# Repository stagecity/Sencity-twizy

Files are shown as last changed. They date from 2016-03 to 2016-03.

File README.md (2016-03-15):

# Sencity-twizy

This repository contains programs, documentation and other stuff needed by the project Sencity to work with the car.
This work is from the school [TELECOM Nanncy](http://telecomnancy.univ-lorraine.fr)

## Sencity project
Sencity is an educational collaborative and innovative project around the Internet of Things and
smart city. It relies on the development of an experimental platform to allow students to design,
develop and test new smart services in interaction with citizens and their environment. As part
of the project, an electric car was bought to collect data across the city.

## Environment 
### Operating system
It is recommanded to use Ubuntu LTS (14.04).
Download it here : http://www.ubuntu.com/download/desktop

Follow the installation instructions : http://www.ubuntu.com/download/desktop/install-ubuntu-desktop

**You will need to use the serial, so ya have to add your user to the group dialout**
 
### Network 
#### LIDAR
The Velodyne LIDAR Puck send data over ethernet with UDP packet.
You will need to set up your ethernet interface as follow :
 * IP address: 192.168.1.70 (70 as example, any number except 201 works)
 * Gateway: 255.255.255.0

**Don't forget to allow incoming UDP packet from 192.168.1.201 in your firewall**

#### GoPro
To remotly control the GoPro, you will need to configure it as a WiFi hotspot and then connect it.
If you use the one that was configured during the internship, use the following login :
 * SSID : TNTwizy1
 * Passphrase (WPA-PSK) : telecom54

#### WiFi
In order to perform WiFi scan with the ROS WiFi module, you need to set the setuid on iwlist :
```bash
chmod +s /sbin/iwlist
```

### Robot Operating System
#### Installation
Robot Operating System is the main component of this work.
Follow intructions from this page : http://wiki.ros.org/indigo/Installation/Ubuntu
You have to install the following dependancies :

```bash
apt-get install  ros-indigo-desktop-full ros-indigo-imu-filter-madgwick ros-indigo-rviz-imu-plugin ros-indigo-nmea-msgs libpcap-dev
```

#### Workspace
To set your workspace up, follow the ROS wiki :
http://wiki.ros.org/ROS/Tutorials/InstallingandConfiguringROSEnvironment

#### To learn
You should learn ROS basis from their Tutorials :
http://wiki.ros.org/ROS/Tutorials

#### Compilation
In the src folder, copy all packages from the folder ROS/.

Then compile them with ROS build system :
```bash
catkin_make -DCMAKE_BUILD_TYPE=RelWithDebInfo gps_msgs_generate_messages wifi_msgs_generate_messages
catkin_make -DCMAKE_BUILD_TYPE=RelWithDebInfo
```

To install files in your workspace use the following command :

```bash
catkin_make -DCMAKE_BUILD_TYPE=RelWithDebInfo install
```
### Install script
To setup your environment, you can just install the Operating system and execute [setup.sh](setup.sh).
```bash
wget "https://github.com/stagecity/Sencity-twizy/raw/master/setup.sh"
chmod +x setup.sh
./setup.sh
```

### Arduino
You will need arduino to read data from the Inertial Measurement Unit
Official website : https://www.arduino.cc/

The recommanded IDE is [Arduino IDE](https://www.arduino.cc/en/Main/Software)

You may want to read its [manual](https://www.arduino.cc/en/Guide/Environment)!

#### Librarie
You will have to copy the folder "Arduino/libraries/MPU9250" as "Mpu9250Spi"in your arduino libraries folder.

#### Compilation
Open the sketch Arduino/imu/imu.ino with arduino IDE and upload it on your board.

## Data specification
see [Data.md](Data.md)

## Hardware specification and configuration
see [Hardware.md](Hardware.md)

## Use
To start the saving system :
ROS only :
```bash
roslaunch twizy save.launch maxSize:=MaximalFileSizeInByte outputDir:=/path/to/record/folder/ wifiPort:=wifiCardName gpsPort:=/dev/tty{ACM|USB}[0-9] imuPort:=/dev/tty{ACM|USB}[0-9]
```
ROS and GoPro acquisition :
```bash
./launch.sh maxSize:=MaximalFileSizeInByte outputDir:=/path/to/record/folder/ wifiPort:=wifiCardName gpsPort:=/dev/tty{ACM|USB}[0-9] imuPort:=/dev/tty{ACM|USB}[0-9]
```

To view the recorded data :
```bash
roslaunch twizy viewBag.launch file:=/path/to/recorde/Rosbag_yyyy-mm-dd-hh-mm-ss.bag
```

You will find more arguments in the ROS twizy package dcumentation.

Other launch files are avaible : 
 * saveAndView.launch : record data and show them in real-time
 * streamView.launch : show sensors data in real-time
 * view.launch : launch ROS viewing software with configurations

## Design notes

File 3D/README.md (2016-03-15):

# 3D Model for printer

This folder contains 3D model made with the software OpenScad.
They are intended to be printed with a 3D printer!

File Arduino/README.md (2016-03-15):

# Arduino work

You will find here libraries and sketches for Arduino that are used in the project.

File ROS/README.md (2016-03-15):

# ROS modules

This folder contains modules for ROS needed or developed for the project.

 * gps, imu, velodyne_savedata and wifi contain modules developed for sensors
 * velodyne is a fork heavily modified for this project
 * velodyne_savedata is a module for velodyne to store LIDAR data in file
 * twizy contains the ROS core of this project
 * rviz_satellite is a module used to see GPS position on OpenStreetMaps maps in rviz
 * serial is a dependancie librarie for gps and imu

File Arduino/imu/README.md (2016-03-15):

# Arduino sketch for IMU

This sketch is intended to collect IMU data with the MPU9250-SPI library and to send it to ROS over serial 

Open it with Arduino IDE and upload to your board

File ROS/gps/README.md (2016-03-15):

# ROS GPS modules

 * gps : metapackage for all this modules
 * gps_msgs : messages definition used by these modules
 * gps_driver : get serial data from GPS and publish NMEA sentences in ROS message
 * gps_parser : parse NMEA sentences and publish data in ROS message
 * gps_fix : publish position-velocity-time fix for ROS

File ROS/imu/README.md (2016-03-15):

# ROS IMU modules

 * imu : metapackage for all this modules
 * imu_driver : get serial data from Arduino and publish ROS messages for IMU
 * imu_save : save IMU data in binary file

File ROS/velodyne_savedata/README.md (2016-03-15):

Overview
========

Velodyne_savedata is a package supporting `Velodyne high
definition 3D LIDAR VLP16`.

It works with and uses the following :

.. _ROS: http://www.ros.org
.. _Velodyne: http://www.ros.org/wiki/velodyne
.. _`Velodyne high definition 3D LIDARs`: http://www.velodynelidar.com/lidar/lidar.aspx

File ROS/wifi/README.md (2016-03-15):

# ROS WiFi modules

 * wifi : metapackage for all this modules
 * wifi_msgs : messages definition used by these modules
 * wifi_driver : get serial data from GPS and publish NMEA sentences in ROS message
 * wifi_save : publish position-velocity-time fix for ROS

**WiFi driver require the software iwlist. The setuid bit must be set!**
By example :
```bash
chmod +s /sbin/iwlist
```

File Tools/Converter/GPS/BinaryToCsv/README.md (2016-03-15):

# GPS binary to CSV tool

This tool is intended to convert saved file from ROS gps_save module to CSV file format.

## How to compil :
```bash
make
```

## How to use :
```bash
./imuBinToCsv /path/to/file.bin
```
The new file will be : /path/to/file.bin.csv
**Be aware that no check is performed to verify the input file is correct!**

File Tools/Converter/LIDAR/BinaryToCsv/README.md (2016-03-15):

# LIDAR binary to CSV tool

This tool is intended to convert saved file from ROS velodyne_savedata module to CSV file format.

## How to compil :
```bash
make
```

## How to use :
```bash
./lidarBinToCsv /path/to/file.bin
```
The new file will be : /path/to/file.bin.csv
**Be aware that no check is performed to verify the input file is correct!**

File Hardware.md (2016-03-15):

# Hardware 
Here is described the hardware.

## Garmin GPS 18 LVC

Seller site : [GPS 18x OEM | Garmin](https://buy.garmin.com/en-US/US/oem/sensors-and-boards/gps-18x-oem/prod27594.html)

[Driver and Software](https://www8.garmin.com/support/collection.jsp?product=010-00321-31)

Please refer to APPENDIX E of [Garmin 18.pdf](Docs/GPS/Garmin 18.pdf), and download [SNSRXCFG](https://www8.garmin.com/support/download_details.jsp?id=4053) to configure the GPS.

### Configuration

Sensor configuration:
 * Earth Datum : WGS 84
 * Fix mode : Automatic
 * Differential mode : Automatic
 * Baud Rate : 38400
 * DGPS Mode : WAAS Only
 * Pulse Per Second : checked
 * Phase Output Data : NOT checked
 * PPS Auto Off Mode : NOT checked
 * Position Averaging : NOT checked
 * NMEA 2.30 Mode : checked

NMEA Sentence Selections :
 * GPRMC
 * GPGGA
 * GPGSA
 * PGRME
 * GPVTG
 * PGRMV
 
### Connection

This sensor is connected to the PC with a Serial Basic Breakout Board. 
The one used in was : [DFRobot FTDI USB to Serial Basic Breakout Board](http://www.robotshop.com/en/dfrobot-ftdi-usb-serial-basic-breakout-board.html)

The signal from the GPS has to be inverted. The [MC74HCO4AN](Docs/GPS/MC74HC04ADT.pdf) hex inverter was used.

Pinout of the GPS is in [Garmin 18.pdf](Docs/GPS/Garmin 18.pdf), section 2.1 GPS 18 LVC & GPS 18-5Hz PINOUT (page 8)

#### Wiring Diagrams

**Note** : The Serial Basic Breakout Board refers RX and TX as the ones of the peripheral board, not its own.

```
+----------------------+                 +-----------------------+-----+
|                   GND|-----------------|GND (black, 2 wires)   | GPS |
|   Serial Basic    VCC|-----------------|VCC (red)              +-----+
|  Breakout Board   RXI|-------|>o-------|RCV (green)                  |
|                   TXD|-------o<|-------|TXD (white)                  |
|                   DCD|-----------------|MPO (yellow, optional)       |
+----------------------+                 +-----------------------------+
```
For a more detailed diagram, with MC74HCO4AN connection, see [wiring.pdf](Docs/GPS/wiring.pdf)

## Drotek IMU 10DOF - MPU9250 + MS5611

Seller site : [Drotek IMU 10DOF - MPU9250 + MS5611](http://www.drotek.com/shop/fr/home/466-imu-10dof-mpu9250-ms5611.html)
This sensor is connected to the Arduino using a Category 5 cable - UDP.

### Connection
####IMU side

```
                       +----------+
                       |()  __  ()|
                       |   [__]   |
       (green)  CS_MS -|o        o|- SDI (blue)
 (green-white)    SDO -|o   ##   o|- SCL (brown-white)
(orange-white)    INT -|o   ##   o|- GND (blue-white)
      (orange) CS_MPU -|o        o|- VDD (brown)
                       | MPU 9250 |
                       |()      ()|
                       +----------+
```

#### Arduino Side

```
                                                 PC
                                                / \
                                                | |
                                              +-----+
                 +----[PWR]-------------------| USB |--+
                 |                            +-----+  |
                 |         GND/RST2  [ ][ ]            |
                 |       MOSI2/SCK2  [ ][ ]  A5/SCL[ ] |
                 |          5V/MISO2 [ ][ ]  A4/SDA[ ] | 
                 |                             AREF[ ] |
                 |                              GND[ ] |
                 | [ ]N/C                    SCK/13[ ] |--- brown-white
                 | [ ]v.ref                 MISO/12[ ] |--- green-white
                 | [ ]RST                   MOSI/11[ ]~|--- blue
                 | [ ]3V3    +---+               10[ ]~|--- orange
        brown ---| [ ]5v     | A |                9[ ]~|--- green
   blue-white ---| [ ]GND   -| R |-               8[ ] |--- orange-white
                 | [ ]GND   -| D |-                    |
                 | [ ]Vin   -| U |-               7[ ] |
                 |          -| I |-               6[ ]~|
                 | [ ]A0    -| N |-               5[ ]~|
                 | [ ]A1    -| O |-               4[ ] |
                 | [ ]A2     +---+           INT1/3[ ]~|
                 | [ ]A3                     INT0/2[ ] |
                 | [ ]A4/SDA  RST SCK MISO     TX>1[ ] |
                 | [ ]A5/SCL  [ ] [ ] [ ]      RX<0[ ] |
                 |            [ ] [ ] [ ]              |
                 |  UNO_R3    GND MOSI 5V  ____________/
                  \_______________________/
```
Arduino ASCII art from [BusyDucks](http://busyducks.com/ascii-art-arduinos)

#### Summary

| Arduino Pin | IMU | Cable's wire color |
|:---:|:---:|:---:|
| 8 | INT | orange-white |
| 9 | CS_MS  | green |
| 10 | CS_MPU | orange |
| 11 (MOSI) | SDA | blue |
| 12 (MISO) | SDO | green-white |
| 13 (SCK) | SCL | brown-white |
| GND | GND | blue-white |
| 5V | VDD | brown |

### Axes
#### Drotek IMU default axes

Accelerometer and gyroscope :
```
           +----------+   Z
          /()  __  ()/    ↺
         /   /__/   /     |
        /o        o/      |
       /o   ##   o/       +-------⤹ Y 
      /o   ##   o/       /
     /o        o/       /
    / MPU 9250 /       ↺
   /()      ()/       X
  +----------+
```
Compass :
```
           +----------+   
          /()  __  ()/    
         /   /__/   /     
        /o        o/      
       /o   ##   o/       +------- X
      /o   ##   o/       /|
     /o        o/       / |
    / MPU 9250 /       Y  Z
   /()      ()/
  +----------+

```

#### ROS
Accelerometer, gyroscope and compass :

```
           +----------+   Z (up)
          /()  __  ()/    ↺
         /   /__/   /     |
        /o        o/      |
       /o   ##   o/       +-------⤹ Y (left)
      /o   ##   o/       /
     /o        o/       /
    / MPU 9250 /       ↺
   /()      ()/       X (front)
  +----------+
```

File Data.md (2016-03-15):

# Sencity-twizy data specification

Here is the data specification of saved files.
The structures of each following section are stored sequentially, so that a file is like an array of structure.

## LIDAR
File name : VLP-16_{unix time, format : seconds.nanoseconds}.bin

```C
typedef struct {
    uint64_t stamp;     /**< ROS timestamp in nano seconds */
    float x;            /**< Forward (relative to car), in meter from LIDAR center */
    float y;            /**< Left (relative to car), in meter from LIDAR center */
    float z;            /**< Up (relative to car), in meter from LIDAR center */
    uint8_t ring;       /**< Velodyne laser number */
    uint8_t intensity;  /**< Laser intensity measured */
} __attribute__((packed)) Point;
```

## GPS
File name : GPS_{unix time, format : seconds.nanoseconds}.bin

```C
typedef struct {
    uint64_t stamp;         /**< ROS timestamp in nano seconds */
    double latitude;        /**< GPS latitude in degrees */
    double longitude;       /**< GPS longitude in degrees */
    float seaHeight;        /**< Height above sea in meters */
    float geoidHeight;      /**< Geoidal height in meters */
    float positionDilutionOfPrecision;      /**< Position dilution of precision */
    float horizontalDilutionOfPrecision;    /**< Horizontal dilution of precision */
    float verticalDilutionOfPrecision;      /**< Vertical dilution of precision */
    float magneticVariation;                /**< Magnetic variation of direction in degrees*/
    float trueCourseOverGround;             /**< True course over ground in degrees */
    float magneticCourseOverGround;         /**< Magnetic course over ground in degrees */
    float speedOverGround;                  /**< Speed over ground in kilometers/hour */
    float estimatedHorizontalPosError;      /**< Estimated horizontal position error in meters */
    float estimatedVerticalPosError;        /**< Estimated vertical position error in meters */
    float estimatedPosError;        /**< Estimated position error in meters */
    float trueEstVelocity;          /**< True est velocity in meters/second */
    float trueNorthVelocity;        /**< True north velocity in meters/second */
    float upVelocity;       /**< Up velocity in meters/second */
    uint8_t gpsQuality;     /**< GPS quality :GPS quality indication, 0 = fix not available, 1 = Non-differential GPS fix available, 2 = Differential GPS (WAAS) fix available, 6 = Estimated */
    uint8_t nbSat;          /**< Number of satellite in view */
    uint8_t gsaModeAuto;    /**< Automatic mode */
    uint8_t fixType;        /**< Fix type, 1 = not available, 2 = 2D, 3 = 3D */
    uint8_t utcHour;        /**< UTC hour */
    uint8_t utcMin;         /**< UTC minute */
    uint8_t utcSec;         /**< UTC second */
    uint8_t validPosition;  /**< is position valid : boolean  */
    uint8_t utcDay;         /**< UTC day */
    uint8_t utcMounth;      /**< UTC mounth */
    uint8_t utcYear;        /**< UTC Year */
    uint8_t mode;           /**< Mode indicator : A = Autonomous, D = Differential, E = Estimated, N = Data not valid */
    uint8_t prnUsed[12];    /**< PRN number, 01 to 32, of satellite used in solution, up to 12 transmitted */
} GpsBinaryData;
```

## IMU
File name : IMU_{unix time, format : seconds.nanoseconds}.bin

```C
typedef struct {
    uint64_t stamp;     /**< ROS timestamp in nanoseconds */
    double accel[3];    /**< 3D accelerometer vector. Composant in meter/second^2 (SI)  */
    double gyro[3];     /**< 3D gyroscope vector. Composant in rad/second  */
    double mag[3];      /**< 3D magnetometer vector. Composant in Tesla */
} ImuBinaryData;
```

This 3D vectors are defined as :
 * vector[0] = x (Forward (relative to car))
 * vector[1] = y (Left (relative to car))
 * vector[2] = z (Up (relative to car))
    
## WiFi
File name : WIFI_{unix time, format : seconds.nanoseconds}.bin
```C
// Char size of MAC address
#define ADDRESS_SIZE    18
// max char size of WiFi SSID
#define SSID_SIZE       30
// Max char size of WiFi security information
#define SECURITY_SIZE   50
// Max char size of security group
#define GROUP_SIZE      20
// Max char size of security pair information
#define PAIR_SIZE       20
// Max char size of protocol information
#define PROTOCOL_SIZE   20

typedef struct {
    uint64_t stamp;                 /**< ROS timestamp in nano seconds */
    uint16_t frequency;             /**< WiFi frequency (channel) in MHz */
    char address[ADDRESS_SIZE];     /**< WiFi access point MAC address */
    char ssid[SSID_SIZE];           /**< WiFi SSID */
    char security[SECURITY_SIZE];   /**< WiFi security protocol */
    char groupCipher[GROUP_SIZE];   /**< WiFi security group cipher */
    char pairwiseCiphers[PAIR_SIZE];/**< WiFi security pair ciphers */
    char protocol[PROTOCOL_SIZE];   /**< WiFi protocol */
    uint8_t signal;                 /**< signal strengh form 0 to 100(highest) */
    uint8_t encryption;             /**< is WiFi encrypted (true is non null) */
} WifiBinaryData;
```

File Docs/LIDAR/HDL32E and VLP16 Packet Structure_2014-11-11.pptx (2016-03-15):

## HDL-32E: Data Packets Structure (Port 2368)

Laser Fire: 0

1248 bytes

42 bytes

Header
42 bytes

12x(2+2+96) = 1200 bytes

Laser Fire: 2
ffee
Horizontal Angle | | 5794
CH 0 | Distance | 2112
| Intensity | 104
CH 1 | Distance | 8672
| Intensity | 8
: : : : | :
| :
CH 31 | Distance | 3676
| Intensity | 24

4 + 2 = 6 bytes

Factory Use
2 bytes
37 21

Timestamp:
Microseconds since
top of the hour
(synced w GPS every sec)
Latched to first firing of the first firing sequence

Laser Fire: 0
ffee
Horizontal Angle | | 5559
CH 0 | Distance | 2112
| Intensity | 104
CH 1 | Distance | 8683
| Intensity | 8
: : : : | :
| :
CH 31 | Distance | 0
| Intensity | 8

Laser Fire: 0
ffee
Horizontal Angle | | 5559
CH 0 | Distance | 2112
| Intensity | 104
CH 1 | Distance | 8683
| Intensity | 8
: : : : | :
| :
| Distance | 0
| Recharge Time

Laser Fire: 1
ffee
Horizontal Angle | | 5576
CH 0 | Distance | 2113
| Intensity | 104
CH 1 | Distance | 8685
| Intensity | 8
: : : : | :
| :
CH 31 | Distance | 0
| Intensity | 8

Laser Fire: 0
ffee
Horizontal Angle | | 5559
CH 0 | Distance | 2112
| Intensity | 104
CH 1 | Distance | 8683
| Intensity | 8
: : : : | :
| :
| Distance | 0
| Recharge Time

- Angle
~0.16˚ @ 10Hz

Laser Fire: 0
ffee
Horizontal Angle | | 5559
CH 0 | Distance | 2112
| Intensity | 104
CH 1 | Distance | 8683
| Intensity | 8
: : : : | :
| :
| Distance | 0
| Recharge Time

- Angle
~0.16˚ @ 10Hz

Laser Fire: 11
ffee
Horizontal Angle | | 5748
CH 0 | Distance | 2110
| Intensity | 104
CH 1 | Distance | 3630
| Intensity | 104
: : : : | :
| :
CH 31 | Distance | 3661
| Intensity | 96

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

Timestamp
4 bytes
1439393982

- 30.67˚

Horizontal
Angle

46.08

32x 1.152us

- 9.33˚

Ch 15 = 0˚

- 9.33˚

Vert Angle | CH
10.67 | 31
9.33 | 29
8 | 27
6.67 | 25
5.33 | 23
4 | 21
2.67 | 19
1.33 | 17
0 | 15
-1.33 | 13
-2.67 | 11
-4 | 9
-5.33 | 7
-6.67 | 5
-8 | 3
-9.33 | 1
-10.67 | 30
-12 | 28
-13.33 | 26
-14.67 | 24
-16 | 22
-17.33 | 20
-18.67 | 18
-20 | 15
-21.33 | 14
-22.67 | 12
-24 | 10
-25.33 | 8
-26.67 | 6
-28 | 4
-29.33 | 2
-30.67 | 0

CH | Vert Angle
0 | -30.67
1 | -9.33
2 | -29.33
3 | -8
4 | -28
5 | -6.67
6 | -26.67
7 | -5.33
8 | -25.33
9 | -4
10 | -24
11 | -2.67
12 | -22.67
13 | -1.33
14 | -21.33
15 | 0
16 | -20
17 | 1.33
18 | -18.67
19 | 2.67
20 | -17.33
21 | 4
22 | -16
23 | 5.33
24 | -14.67
25
26 | -13.33
27 | 8
28 | -12
29 | 9.33
30 | -10.67
31 | 10.67

8x 1.152us

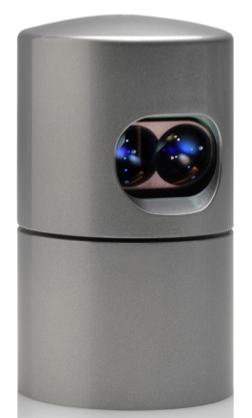
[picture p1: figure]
UDL-32E

Vertical Angle

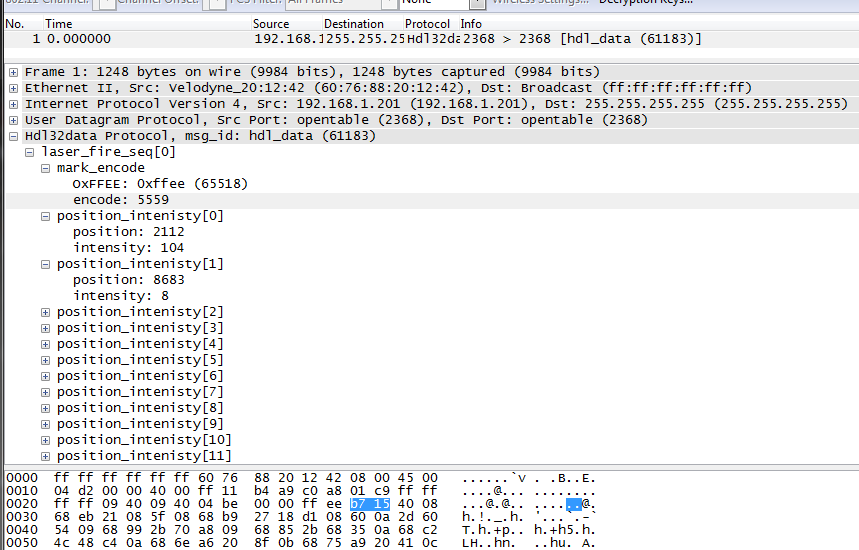
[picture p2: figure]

Laser Fire: 1

Laser Fire: 2

12x 46.08 us = 552.96 us

## VLP-16: Data Packets Structure (Port 2368)

Laser Fire: 0

1248 bytes

42 bytes

Header
42 bytes

12x(2+2+96) = 1200 bytes

Laser Fire: 2
ffee
Horizontal Angle | | 5794
CH 0 | Distance | 2112
| Intensity | 104
CH 1 | Distance | 8672
| Intensity | 8
: : : : | :
| :
CH 15 | Distance | 3676
| Intensity | 24

4 + 2 = 6 bytes

Factory Use
2 bytes
37 21

Timestamp:
Microseconds since
top of the hour
(synced w GPS every sec)
Latched to first firing of the first firing sequence

Laser Fire: 0
ffee
Horizontal Angle | | 5559
CH 0 | Distance | 2112
| Intensity | 104
CH 1 | Distance | 8683
| Intensity | 8
: : : : | :
| :
CH 15 | Distance | 0
| Intensity | 8

Laser Fire: 1
ffee
Horizontal Angle | | 5576
CH 0 | Distance | 2113
| Intensity | 104
CH 1 | Distance | 8685
| Intensity | 8
: : : : | :
| :
CH 15 | Distance | 0
| Intensity | 8

Laser Fire: 11
ffee
Horizontal Angle | | 5748
CH 0 | Distance | 2110
| Intensity | 104
CH 1 | Distance | 3630
| Intensity | 104
: : : : | :
| :
CH 15 | Distance | 3661
| Intensity | 96

Timestamp
4 bytes
1439393982

16x 2x 1.152us
= 36.864us

110.592us

8x 2x 1.152us
= 18.432us

Laser Fire: 0
ffee
Recharge (no angle info)
CH 0 | Distance | 2112
| Intensity | 104
CH 1 | Distance | 8683
| Intensity | 8
: : : : | :
| :
CH 15 | Distance | 0
| Intensity | 8

Laser Fire: 0
ffee
Recharge (no angle info)
CH 0 | Distance | 2112
| Intensity | 104
CH 1 | Distance | 8683
| Intensity | 8
: : : : | :
| :
CH 15 | Distance | 0
| Intensity | 8

Vert Angle | CH
+15 | +15
+13 | +13
+11 | +11
+9 | +9
+7 | 7
+5 | 5
-+3 | 3
+1 | 1
-1 | 14
-3 | 12
-5 | 10
-7 | 8
-9 | 6
-11 | 4
-13 | 2
-15 | 0

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

Laser Fire: 1

Laser Fire: 2

Vertical Angle

16x 2x 1.152us

8x 2x 1.152us

12x 110.592 us = 1.327.104 ms

## HDL-32E and VLP-16: Laser Firing Timing Tables

| | Laser (DSR #)
| | 0 | 1 | 2 | 3 | 4 | 5 | 6 | 7 | 8 | 9 | 10 | 11 | 12 | 13 | 14 | 15 | 16 | 17 | 18 | 19 | 20 | 21 | 22 | 23 | 24 | 25 | 26 | 27 | 28 | 29 | 30 | 31
Firing Block | 0 | 0 | 1 | 2 | 3 | 5 | 6 | 7 | 8 | 9 | 10 | 12 | 13 | 14 | 15 | 16 | 17 | 18 | 20 | 21 | 22 | 23 | 24 | 25 | 26 | 28 | 29 | 30 | 31 | 32 | 33 | 35 | 36
| 1 | 46 | 47 | 48 | 50 | 51 | 52 | 53 | 54 | 55 | 56 | 58 | 59 | 60 | 61 | 62 | 63 | 65 | 66 | 67 | 68 | 69 | 70 | 71 | 73 | 74 | 75 | 76 | 77 | 78 | 79 | 81 | 82
| 2 | 92 | 93 | 94 | 96 | 97 | 98 | 99 | 100 | 101 | 103 | 104 | 105 | 106 | 107 | 108 | 109 | 111 | 112 | 113 | 114 | 115 | 116 | 118 | 119 | 120 | 121 | 122 | 123 | 124 | 126 | 127 | 128
| 3 | 138 | 139 | 141 | 142 | 143 | 144 | 145 | 146 | 147 | 149 | 150 | 151 | 152 | 153 | 154 | 156 | 157 | 158 | 159 | 160 | 161 | 162 | 164 | 165 | 166 | 167 | 168 | 169 | 170 | 172 | 173 | 174
| 4 | 184 | 185 | 187 | 188 | 189 | 190 | 191 | 192 | 194 | 195 | 196 | 197 | 198 | 199 | 200 | 202 | 203 | 204 | 205 | 206 | 207 | 209 | 210 | 211 | 212 | 213 | 214 | 215 | 217 | 218 | 219 | 220
| 5 | 230 | 232 | 233 | 234 | 235 | 236 | 237 | 238 | 240 | 241 | 242 | 243 | 244 | 245 | 247 | 248 | 249 | 250 | 251 | 252 | 253 | 255 | 256 | 257 | 258 | 259 | 260 | 262 | 263 | 264 | 265 | 266
| 6 | 276 | 278 | 279 | 280 | 281 | 282 | 283 | 285 | 286 | 287 | 288 | 289 | 290 | 291 | 293 | 294 | 295 | 296 | 297 | 298 | 300 | 301 | 302 | 303 | 304 | 305 | 306 | 308 | 309 | 310 | 311 | 312
| 7 | 323 | 324 | 325 | 326 | 327 | 328 | 329 | 331 | 332 | 333 | 334 | 335 | 336 | 338 | 339 | 340 | 341 | 342 | 343 | 344 | 346 | 347 | 348 | 349 | 350 | 351 | 353 | 354 | 355 | 356 | 357 | 358
| 8 | 369 | 370 | 371 | 372 | 373 | 374 | 376 | 377 | 378 | 379 | 380 | 381 | 382 | 384 | 385 | 386 | 387 | 388 | 389 | 391 | 392 | 393 | 394 | 395 | 396 | 397 | 399 | 400 | 401 | 402 | 403 | 404
| 9 | 415 | 416 | 417 | 418 | 419 | 420 | 422 | 423 | 424 | 425 | 426 | 427 | 429 | 430 | 431 | 432 | 433 | 434 | 435 | 437 | 438 | 439 | 440 | 441 | 442 | 444 | 445 | 446 | 447 | 448 | 449 | 450
| 10 | 461 | 462 | 463 | 464 | 465 | 467 | 468 | 469 | 470 | 471 | 472 | 473 | 475 | 476 | 477 | 478 | 479 | 480 | 482 | 483 | 484 | 485 | 486 | 487 | 488 | 490 | 491 | 492 | 493 | 494 | 495 | 497
| 11 | 507 | 508 | 509 | 510 | 511 | 513 | 514 | 515 | 516 | 517 | 518 | 520 | 521 | 522 | 523 | 524 | 525 | 526 | 528 | 529 | 530 | 531 | 532 | 533 | 535 | 536 | 537 | 538 | 539 | 540 | 541 | 543
| | Notes:
| | All times in microseconds. Combine the value shown from the packet timestamp (microseconds from the top of the hour), to arrive at actual laser firing time.
| | Rotary Encoder and Timestamp values are read at the beginning of packet creation at actual laser firing time.
| | Firing Block can be determined by the packet offset (in bytes decimal) divided by 100.
| | Formula to determine timing is: (Firing Block * 46.08) + (DSR# * 1.152).

| | Laser (DSR #)
| | First Firing | | | | | | | | | | | | | | | | Second Firing
| | 0 | 1 | 2 | 3 | 4 | 5 | 6 | 7 | 8 | 9 | 10 | 11 | 12 | 13 | 14 | 15 | 0 | 1 | 2 | 3 | 4 | 5 | 6 | 7 | 8 | 9 | 10 | 11 | 12 | 13 | 14 | 15
Data Block | 0 | 0 | 2 | 5 | 7 | 9 | 12 | 14 | 16 | 18 | 21 | 23 | 25 | 28 | 30 | 32 | 35 | 55 | 58 | 60 | 62 | 65 | 67 | 69 | 71 | 74 | 76 | 78 | 81 | 83 | 85 | 88 | 90
| 1 | 111 | 113 | 115 | 118 | 120 | 122 | 124 | 127 | 129 | 131 | 134 | 136 | 138 | 141 | 143 | 145 | 166 | 168 | 170 | 173 | 175 | 177 | 180 | 182 | 184 | 187 | 189 | 191 | 194 | 196 | 198 | 200
| 2 | 221 | 223 | 226 | 228 | 230 | 233 | 235 | 237 | 240 | 242 | 244 | 247 | 249 | 251 | 253 | 256 | 276 | 279 | 281 | 283 | 286 | 288 | 290 | 293 | 295 | 297 | 300 | 302 | 304 | 306 | 309 | 311
| 3 | 332 | 334 | 336 | 339 | 341 | 343 | 346 | 348 | 350 | 353 | 355 | 357 | 359 | 362 | 364 | 366 | 387 | 389 | 392 | 394 | 396 | 399 | 401 | 403 | 406 | 408 | 410 | 412 | 415 | 417 | 419 | 422
| 4 | 442 | 445 | 447 | 449 | 452 | 454 | 456 | 458 | 461 | 463 | 465 | 468 | 470 | 472 | 475 | 477 | 498 | 500 | 502 | 505 | 507 | 509 | 511 | 514 | 516 | 518 | 521 | 523 | 525 | 528 | 530 | 532
| 5 | 553 | 555 | 558 | 560 | 562 | 564 | 567 | 569 | 571 | 574 | 576 | 578 | 581 | 583 | 585 | 588 | 608 | 611 | 613 | 615 | 617 | 620 | 622 | 624 | 627 | 629 | 631 | 634 | 636 | 638 | 641 | 643
| 6 | 664 | 666 | 668 | 670 | 673 | 675 | 677 | 680 | 682 | 684 | 687 | 689 | 691 | 694 | 696 | 698 | 719 | 721 | 723 | 726 | 728 | 730 | 733 | 735 | 737 | 740 | 742 | 744 | 746 | 749 | 751 | 753
| 7 | 774 | 776 | 779 | 781 | 783 | 786 | 788 | 790 | 793 | 795 | 797 | 799 | 802 | 804 | 806 | 809 | 829 | 832 | 834 | 836 | 839 | 841 | 843 | 846 | 848 | 850 | 852 | 855 | 857 | 859 | 862 | 864
| 8 | 885 | 887 | 889 | 892 | 894 | 896 | 899 | 901 | 903 | 905 | 908 | 910 | 912 | 915 | 917 | 919 | 940 | 942 | 945 | 947 | 949 | 952 | 954 | 956 | 958 | 961 | 963 | 965 | 968 | 970 | 972 | 975
| 9 | 995 | 998 | 1000 | 1002 | 1005 | 1007 | 1009 | 1011 | 1014 | 1016 | 1018 | 1021 | 1023 | 1025 | 1028 | 1030 | 1051 | 1053 | 1055 | 1058 | 1060 | 1062 | 1064 | 1067 | 1069 | 1071 | 1074 | 1076 | 1078 | 1081 | 1083 | 1085
| 10 | 1106 | 1108 | 1111 | 1113 | 1115 | 1117 | 1120 | 1122 | 1124 | 1127 | 1129 | 1131 | 1134 | 1136 | 1138 | 1140 | 1161 | 1164 | 1166 | 1168 | 1170 | 1173 | 1175 | 1177 | 1180 | 1182 | 1184 | 1187 | 1189 | 1191 | 1193 | 1196
| 11 | 1217 | 1219 | 1221 | 1223 | 1226 | 1228 | 1230 | 1233 | 1235 | 1237 | 1240 | 1242 | 1244 | 1246 | 1249 | 1251 | 1272 | 1274 | 1276 | 1279 | 1281 | 1283 | 1286 | 1288 | 1290 | 1293 | 1295 | 1297 | 1299 | 1302 | 1304 | 1306
| | Notes:
| | All times in microseconds. Combine the value shown from the packet timestamp (microseconds from the top of the hour), to arrive at actual laser firing time.
| | Rotary Encoder and Timestamp values are read at the beginning of packet creation at actual laser firing time.
| | Data Block can be determined by the packet offset (in bytes decimal) divided by 100.
| | Formula to determine timing is: (Data Block * 110.592) + (DSR# * 2.304). Add 55.296 for the second firing in a data block.

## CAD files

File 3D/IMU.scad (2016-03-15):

/* 
 * Copyright (C) 2015  TELECOM Nancy
 *
 * This model is under the Creative Common CC-BY-SA-NC license.
 *
 */

boardLength             = 22.5;
boardWidth              = 19.5;
boardHeight             = 4.5;

boardGap                = 5;

screwHoleDiam           = 3;
screwSpaceFromEdge      = 1;
screwEp                 = 2;
screwDiam               = 2;

fixationLength          = 20;

epaisseur               = 3;
hauteurBoite            = 25;
filDiam                 = 4;


elevationCarte          = hauteurBoite - boardGap - epaisseur;
baseLength              = boardLength + 2 * (boardGap + epaisseur);
baseWidth               = boardWidth + 2 * (boardGap + epaisseur);

screwCylDiff            = epaisseur + boardGap + screwSpaceFromEdge + screwHoleDiam/2;

diamVisFix              = 4;

fn = 100;

cube(size = [baseLength, baseWidth,  epaisseur]);

//triangle haut
translate([0, baseWidth, 0])
    difference() {
            polyhedron(
                points = [
                          [0, 0, 0], [baseLength/2, fixationLength,0], [baseLength, 0, 0],
                          [0, 0, epaisseur], [baseLength/2, fixationLength,epaisseur], [baseLength, 0, epaisseur]
                         ],
                faces = [
                          [0, 2, 1], [3, 4, 5], [0, 1, 4,3],
                          [0, 3, 5, 2], [1, 2, 5, 4]
                        ]
            );
            translate([baseLength / 2, fixationLength / 2.5, -0.1])
                cylinder(h = epaisseur + 0.2, d = diamVisFix, $fn = fn);
        }
    
 //triangle bas
rotate([180, 0, 0])
    translate([0, 0, -epaisseur])
        difference() {
            polyhedron(
                points = [
                          [0, 0, 0], [baseLength/2, fixationLength,0], [baseLength, 0, 0],
                          [0, 0, epaisseur], [baseLength/2, fixationLength,epaisseur], [baseLength, 0, epaisseur]
                         ],
                faces = [
                          [0, 2, 1], [3, 4, 5], [0, 1, 4,3],
                          [0, 3, 5, 2], [1, 2, 5, 4]
                        ]
            );
            translate([baseLength / 2, fixationLength / 2.5, -0.1])
                cylinder(h = epaisseur + 0.2, d = diamVisFix, $fn = fn);
        }
//face gauche
difference() {
    cube(size = [epaisseur, baseWidth, hauteurBoite]);
    
    translate([epaisseur/2, epaisseur / 2, 0.1])
            cylinder(h = hauteurBoite, d = 1, $fn = fn);
    
    translate([epaisseur/2, baseWidth - epaisseur / 2, 0.1])
            cylinder(h = hauteurBoite, d = 1, $fn = fn);
    
    translate([-0.1, baseWidth / 2, epaisseur + filDiam])
        union() {
            translate([0, -filDiam / 2, 0])
                cube(size = [epaisseur + 0.2, filDiam, hauteurBoite - epaisseur - filDiam + .01]);
            rotate([0, 90, 0])
                cylinder(h = epaisseur + 0.2, d = filDiam, $fn = fn);
            
        }
    
}
//face droite
translate([baseLength - epaisseur, 0, 0]) {
    difference() {
        cube(size = [epaisseur, baseWidth, hauteurBoite]);
         translate([epaisseur/2, epaisseur / 2, 0.1])
            cylinder(h = hauteurBoite, d = 1, $fn = fn);
    
        translate([epaisseur/2, baseWidth - epaisseur / 2, 0.1])
                cylinder(h = hauteurBoite, d = 1, $fn = fn);
    }
}

    
//face bas
translate([epaisseur, 0, 0])
    cube(size = [baseLength - 2 * epaisseur, epaisseur, hauteurBoite]);

//face haut
translate([epaisseur, baseWidth - epaisseur, 0])
    cube(size = [baseLength - 2 * epaisseur, epaisseur, hauteurBoite]);

//Bas gauche
translate( [ screwCylDiff, screwCylDiff, epaisseur])
    difference () {
        cylinder(h = elevationCarte, d = screwHoleDiam + screwEp, $fn = fn);
        cylinder(h = elevationCarte + 0.1, d = screwDiam, $fn = fn);
    }

//bas droite
translate( [ baseLength - screwCylDiff, screwCylDiff, epaisseur])
    difference () {
        cylinder(h = elevationCarte, d = screwHoleDiam + screwEp, $fn = fn);
        cylinder(h = elevationCarte + 0.1, d = screwDiam, $fn = fn);
    }

// haut droite
translate( [ baseLength - screwCylDiff, baseWidth - screwCylDiff, epaisseur])
    difference () {
        cylinder(h = elevationCarte, d = screwHoleDiam + screwEp, $fn = fn);
        cylinder(h = elevationCarte + 0.1, d = screwDiam, $fn = fn);
    }
 
 // haut gauche
translate( [ screwCylDiff, baseWidth - screwCylDiff, epaisseur])
    difference () {
        cylinder(h = elevationCarte, d = screwHoleDiam + screwEp, $fn = fn);
        cylinder(h = elevationCarte + 0.1, d = screwDiam, $fn = fn);
    }

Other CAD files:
3D/IMU_couvercle.scad

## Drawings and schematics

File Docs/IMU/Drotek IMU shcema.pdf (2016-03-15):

## REGUL3.3V

C6

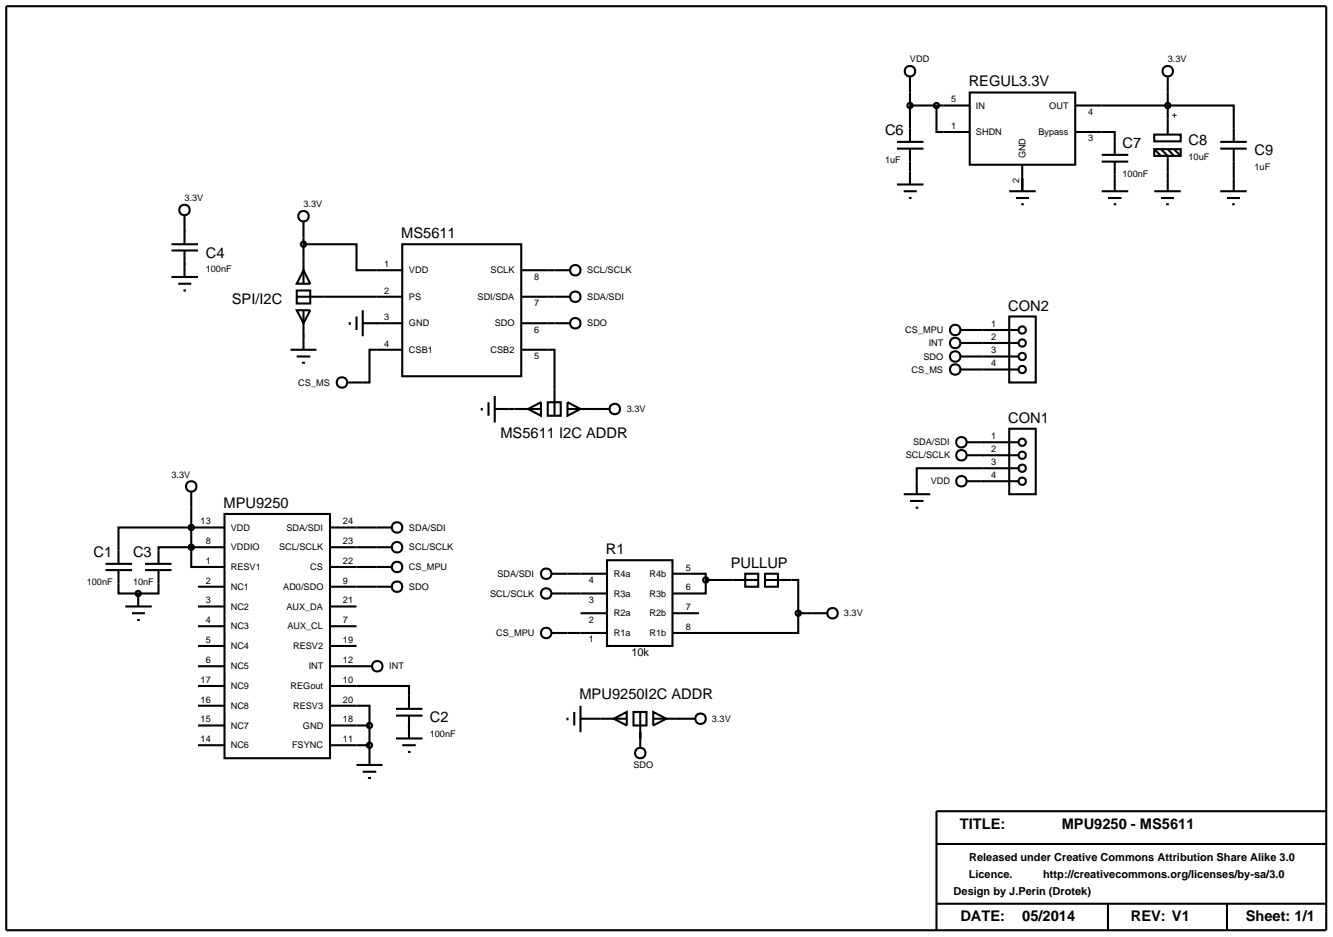
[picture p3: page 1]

Released under Creative Commons Attribution Share Alike 3.0
Design by J.Perin (Drotek)

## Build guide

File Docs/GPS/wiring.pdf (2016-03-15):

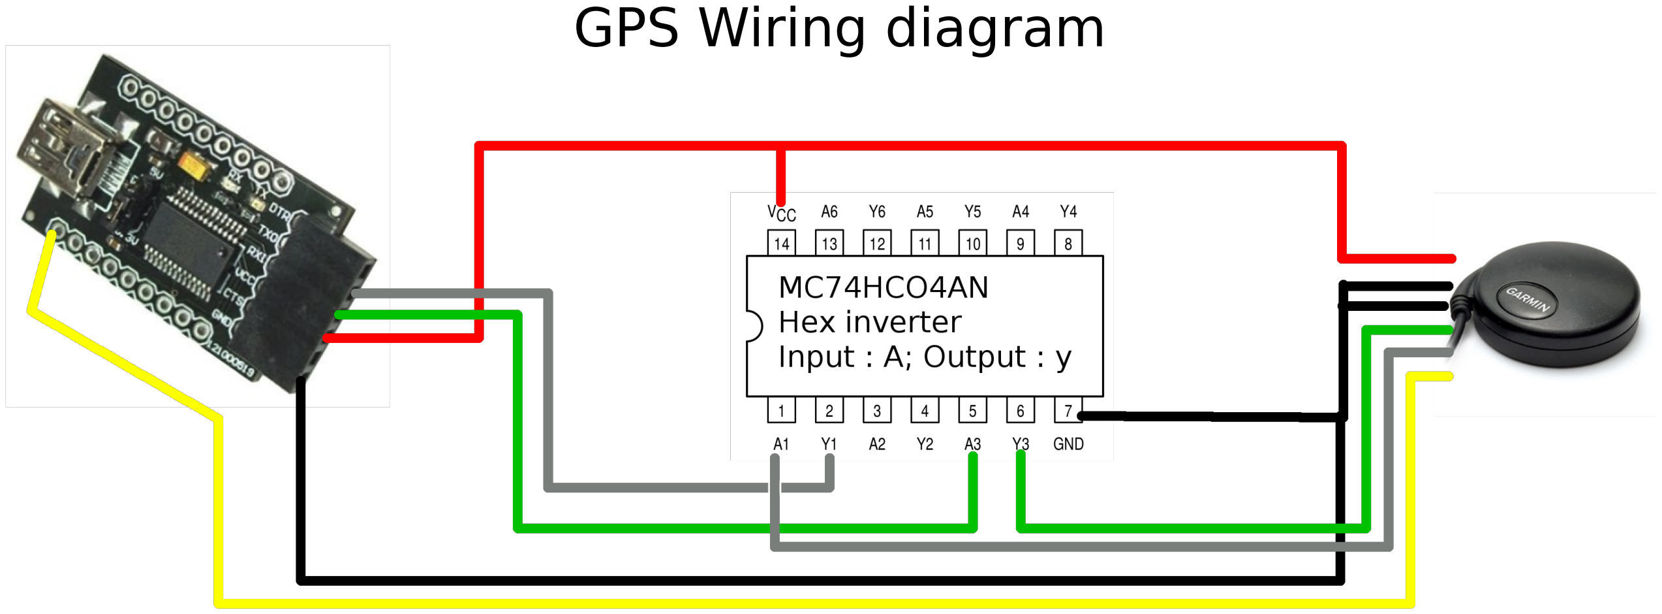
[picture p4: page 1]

GPS Wiring diagram

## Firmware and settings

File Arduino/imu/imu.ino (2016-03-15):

/*
 * Copyright (C) 2015  TELECOM Nancy
 *
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
 * You should have received a copy of the GNU General Public License
 * along with this program.  If not, see <http://www.gnu.org/licenses/>.
 */


#include <SPI.h>

#include "Mpu9250Spi.hpp"


/**
 * @brief Prefix serial data
 */
#define SERIAL_HEADER 0xA5

/**
 * @brief MPU9250 SPI slave select pin connection
 */
int _slaveSelectMpu = 10;
/**
 * @brief Altimeter SPI slave select pin connection
 */
int _slaveSelectAlt = 9;
/**
 * @brief MPU9250 interrupt pin connection
 */
int _mpuInt = 8;

/**
 * @brief MPU9250 with SPI support
 */
mpu9250::Mpu9250Spi mpu(_slaveSelectMpu, _mpuInt);

namespace sketch {

    /**
    * @brief MPU9250 data as either uint8_t array or 3d vectors
    *
    *
    */
    union {
        /**
        * @brief MPU9250 data in 3D Vectors
        *
        *
        */
        struct {
            struct mpu9250::Int16Vect3D accel; /**< 3D accelerometer vector (arbitrary unit) */
            struct mpu9250::Int16Vect3D gyro; /**< 3D gyroscope vector (arbitrary unit) */
            struct mpu9250::Int16Vect3D mag; /**< 3D magnetometer vector (arbitrary unit) */
            int16_t temp; /**< MPU9250 temperature (arbitrary unit) */
        };
        uint8_t value[20]; /**< Structure as array of byte */
    } data;
}


void setup() {
    // Altimeter no used
    pinMode(_slaveSelectAlt, OUTPUT);
    digitalWrite(_slaveSelectAlt, HIGH);

    // Serial at 1Mbauds
    Serial.begin(1000000);
    // Init MPU2950
    mpu.init();
    // Set accelerometer low pass filter to 41Hz
    mpu.setAccelDLPF(true, mpu9250::DLPF_ACCEL_41HZ);
    // Set accelerometer full scale to +- 4G to avoid overflow
    mpu.setAccelFullScale(mpu9250::ACCEL_FULL_SCALE_4G);
    // Set gyroscope low pass filter to 41Hz
    mpu.setGyroDLPF(mpu9250::FCHOICE_DLPF_ENABLE, mpu9250::DLPF_GYRO_41HZ);
    // Set gyroscope full scale to +- 250 degrees/s
    mpu.setGyroFullScale(mpu9250::GYRO_FULL_SCALE_250DPS);
    // We want a sample at 100 Hz (1kHz / (1 + 9))
    mpu.setSampleRateDivider(0x09);
    // Enable interrupt only for data ready
    mpu.setInterrupt(false, false,true, true);
    // Interrupt pin goes LOW only when a read occurs
    mpu.setInterruptPin(false,false, false, true);
    // Send config to MPU9250
    mpu.uploadConfig();
}


void loop() {
    // Check if data ready
    if(digitalRead(_mpuInt) == HIGH) {
        // Get MPU9250 data
        mpu.getSensors(&sketch::data.accel, &sketch::data.gyro, &sketch::data.mag, &sketch::data.temp) ;
        // Write it to serial
        writeSerial();
    }
}

/**
 * @brief write the data structure to the serial port
 *
 *
 */
void writeSerial() {

    uint8_t sum = 0; // checksum initialisation

    // Compute checksum
    // XOR between each byte
    for(uint8_t i = 0; i< 20; i++) {
        sum ^= sketch::data.value[i];
    }

    // Send serial prefix
    Serial.write(SERIAL_HEADER);
    // Send data
    Serial.write(sketch::data.value, 20);
    // Sen checksum
    Serial.write(sum);

}

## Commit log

2016-03-15 Initial release
    [HDL32E and VLP16 Packet Timing.xlsx, IMU.scad, IMU_couvercle.scad]
2016-03-18 Fix : WiFi driver crashed after a while forgot to close a pipe file descriptor

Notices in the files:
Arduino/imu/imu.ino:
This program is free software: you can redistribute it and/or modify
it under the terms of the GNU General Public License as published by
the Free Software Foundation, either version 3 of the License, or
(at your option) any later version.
